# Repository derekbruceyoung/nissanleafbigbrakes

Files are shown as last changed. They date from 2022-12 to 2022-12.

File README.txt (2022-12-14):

BIG BRAKES How to: 355mm 370Z Sport Brakes on AZE0

Now here's something no one has asked for, and your Leaf probably doesn't need this upgrade, but if you run 18" wheels and want to fill them with brakes, this is easy and cheap.

I needed to upgrade the front brakes on my 280hp moto-ICE hybrid Leaf as I intend to track it, and I wanted more confidence that the car could stop its 3750lb bulk when doing spirited back road drives downhill.

After a deep false start on a high $$ solution (including custom CNC machine brackets and radial Brembos), I ended up with an budget all-OEM package that is nearly Bolt in.  I would have liked to have gone with something that I could fit 17s over, but this was too easy and cheap to pass up.

Calipers: 4-pot Akebono "sport" calipers from a 370Z or G37.  Rebuilt units can be had for <$150 on Amazon. 

Brake lines: Stock Leaf lines work, but you need a shorter banjo bolt, which can be found here: https://www.tunerzstore.com/banjo-bolt- ... o-caliper/

Rotors: This was the trickiest part as the 355x32mm 370Z rotors do not have the correct offset.  After some deep digging I found some V8 mustang units that are really close to perfect, and are cheap and available.  Raybestos 680497 or Centric 120.61089 is the part number you're after. There are even reasonably priced 2-piece units available if you want to get fancy: https://kohrmotorsports.com/product/07- ... otor-pair/

Custom Parts:  The calipers Bolt right on, but the rotors need a little help as 1) the center bore is 3mm too big, 2) the offset is 1mm off and 3) the Mustang wheel lugs are M14. To solve this I used sendcutsend.com to make two 1mm thick 6061 spacers that go between the rotor and hub, and ten 15.2m OD, 12.5mm ID rings out of 1/4" Stainless steel to fill in the M14 bores.  I hand bent a 8mm wide strip of 1/16" (1.5mm) aluminum into a ring that takes up the center bore clearance.  I initially tried to design a hub centering feature into the hub spacer (see the photos) and it would have worked except I needed a 1mm thick spacer and a 1.5mm thick ring, so it needed to be two parts.  Total cost of these bits would be less than SCS's $30 minimum order. .DXFs for these parts can be found on Github: https://github.com/derekbruceyoung/nissanleafbigbrakes

Custom Parts BOM (apology for mixing units, but that's just how it is in my life):
2X 0.0625 in aluminum for centerbore ring.DXF -- Material 1.5mm/0.0625 bendable aluminum (this could be made with shears, it's just a strip of aluminum that you need to form into a ring)
10X 0.250 inch SS brake lug hole shim.DXF -- Material 1/4-5/16" (6-8mm) stainless steel
2X 1mm Thick Hub Spacer.DXF -- Material: 1mm/0.040" aluminum or stainless steel

Installation: Everything bolts up and clears -- the only part of the car that needs modification is the splash shield needs trimming -- I just used a pair of sheet metal shears.

I decided to use EBC Yellow stuff pads front and rear (rears are stock IS350 brakes) and flushed the old fluid out and replaced it with Motul RBF 600.

This past weekend I drove the car from a friend's house in Thousand Oaks to the Petersen Museum for the Autopia 2099 show and on the way I hit one of my all time favorite roads, Tuna Canyon in the Malibu hills.  It's a narrow, bumpy 1-way (!) canyon road that descends 1500' in about 3 miles.  The brakes got a little smelly by the end (they were still bedding in) but the grip was fantastic throughout and I was able to be confident I wouldn't fade them and drive off a cliff.  Oh and they look FANTASTIC.  Hooray!

Photos: https://photos.app.goo.gl/J9g8fFkc3bU8k2WH8

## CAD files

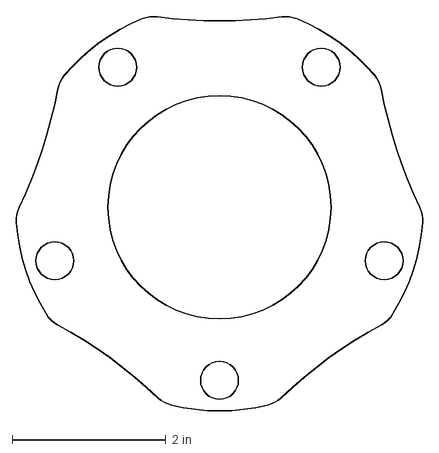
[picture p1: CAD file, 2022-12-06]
1mm Thick Hub Spacer.DXF
5.29 x 5.15 in

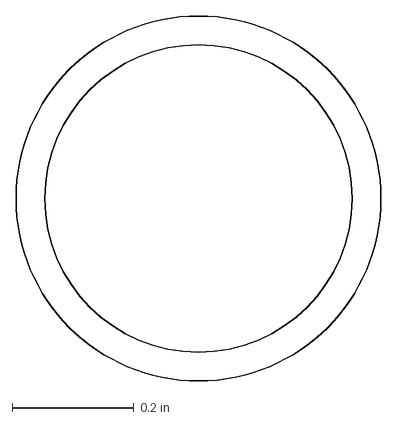
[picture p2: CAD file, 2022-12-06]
0.250 inch SS brake lug hole shim.DXF
0.598 x 0.598 in

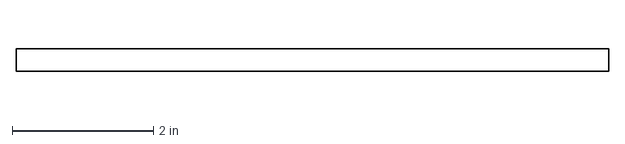
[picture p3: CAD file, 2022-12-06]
0.0625 in aluminum for centerbore ring.DXF
8.39 x 0.315 in
